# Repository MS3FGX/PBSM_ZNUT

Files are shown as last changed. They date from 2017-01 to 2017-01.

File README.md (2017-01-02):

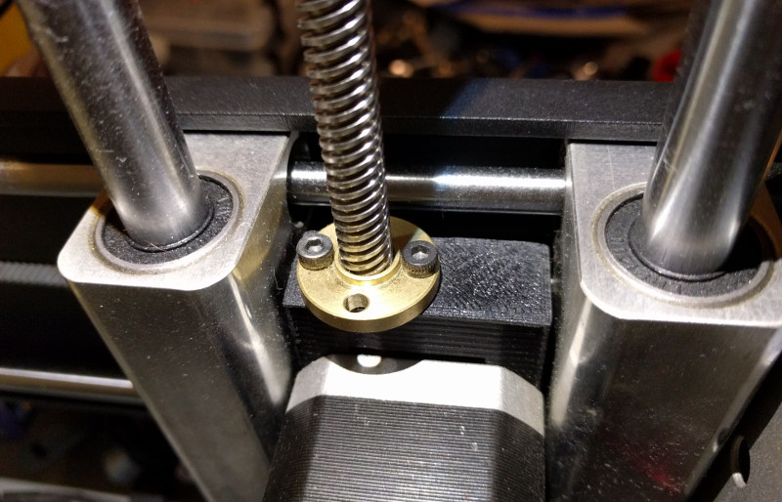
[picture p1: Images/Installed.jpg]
installed


# PrintrBot Simple Metal Metric Z Conversion
With the PrintrBot Simple Metal approaching end of life, I've been thinking ahead in terms of replacement parts. Most of the parts on the PrintrBot are fairly generic or can at least be (relatively) easily swapped out with industry standard components, but one part that really worried me was the Delrin Z nut. This is one of the only parts on the printer that is both proprietary and consumable; eventually the nut will wear down and will need to be replaced.

Rather than buying a bunch of them to stock up for the future (though at the time of this writing, they are no longer available on the PrintrBot store anyway), I decided to replace the Z movement with a standard 8 mm lead screw that can easily be sourced online for a few dollars.

Beyond maintenance and availability issues, converting the PrintrBot's Z motion to metric can (in theory) improve print quality as the controller doesn't have to convert the metric dimensions of the printed part to the PrintrBot's original imperal threaded rod.

# Required Parts
* M3X15mm Cap Screws (x2)
* M3 Nut (x1)
* Brass T8 nut
* 250mm T8 Lead Screw
* 5mmx8mm Coupler (Either printed or purchased)

### Notes:
* Ideally you should get a T8 lead screw that includes a matching nut, but they can be purchased separately if you already have the lead screw.

* If you don't want to buy a Z coupler you can print it, [such as this one from FABlab Moebius](http://www.thingiverse.com/thing:533928).

* Don't be fooled by the length of the original threaded rod (~190mm), with the adapter the Z nut is now above the Y stepper instead of below it, so you need a lead screw that is significantly longer. Otherwise you'll drive the Y arm right off the lead screw if you tried to print something too high.

# Installation
After printing the adapter, press the M3 nut into the bottom and then use the two M3 screws to secure the brass Z nut to the top.

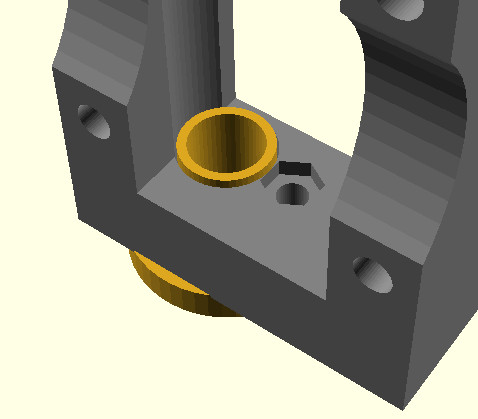
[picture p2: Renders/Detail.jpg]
detail


Once you're sure the brass Z nut fits into the adapter, you can remove the PrintrBot's Y arm, Y belt, and Y stepper. You can then remove the two white spacers, Delrin Z nut, 5mm threaded rod, and Z coupling. They will no longer be required, but I would keep them to be safe.

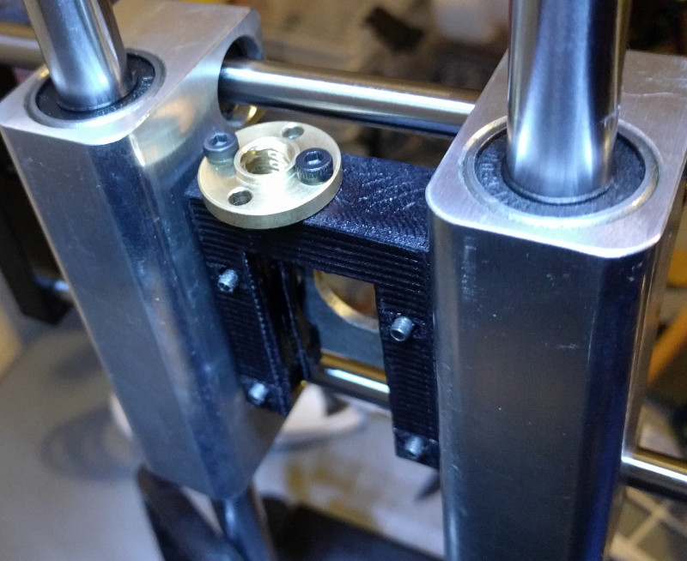
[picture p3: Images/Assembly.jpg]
assembly


Install the adapter and Z nut in place of the original parts, then thread the lead screw through the top of the brass Z nut and down into the new Z coupling.

> **Note**: I found the easiest way to get everything aligned properly was to leave the stepper screws lose while seating the Z coupling and lead screw. Once the coupling and screw are installed properly, then tighten up the stepper screws.

Finally, put the Y stepper and belt back on, making sure that the belt isn't rubbing on the aluminum bearing block (you may need to move the sprocket slightly on the shaft). Also check the belt tightness before putting the Y arm back on.

# Firmware
With the new lead screw installed, you'll need to adjust the printer's firmware so that the steps-per-mm matches the new thread. You can use the [very handy RepRap Calculator](http://www.prusaprinters.org/calculator/#stepspermmlead), but assuming you got a standard 4 start T8 lead screw the steps will need to be set to 400.

To do that, you'll need to connect to the printer with your software of choice and execute the M92 code in the GCode input field. You'll then need to save it to the EEPROM with M500:

```
M92 Z400.00
M500
```

You can then check to make sure it was saved by running M501:

M501

At that point the new values should be active, but I've found in the past it's wise to completely reboot the PrintrBot to make sure firmware settings take.

# Recalibrate Z Offset
After doing so much fiddling with the Z axis, you'll almost certainly need to recalibrate your offset. [Follow the official calibration process](https://www.youtube.com/watch?v=jpmgI4OGldw), and you should be good to do some test prints.

# Auto-Level Warning
As a side effect of this modification, the Z axis movement is now so smooth that the Y arm can actually slide down the rods from just its own weight.

This isn't really a problem normally, but I've found that if you then try and disable the PrintrBot's auto-leveling routine, the arm can actually fall back down while printing. This is evident by smashed up layers and the nozzle occasionally hitting the print. The issue appears to be that the controller turns off the Z stepper between layer changes unless the auto-leveling is actively moving it around.

The easy solution is to just not disable the auto-level routine. The "proper" solution appears to be editing the firmware to tell it to always keep the Z stepper energized; but unless you _really_ want to turn off the leveling, it probably isn't worth it.

# Modifications
The OpenSCAD source is included if you need to make any tweaks to the adapter, but you'll need to drop the ["nutsnbolts" OpenSCAD library](https://github.com/JohK/nutsnbolts) into the current directory before it will compile.

# Acknowledgements
- Makes use of Johannes Kneer's fantastic "nutsnbolts" library.
- Inspired by a design posted by ["aricnorine" on YouImagine](https://www.youmagine.com/designs/printrbot-simple-metal-z-axis-block-for-8mm-metric-coupler).

# License
This program is free software; you can redistribute it and/or modify it under the terms of the GNU General Public License version 3 as published by the Free Software Foundation.



This program is distributed in the hope that it will be useful, but WITHOUT ANY WARRANTY; without even the implied warranty of MERCHANTABILITY or FITNESS FOR A PARTICULAR PURPOSE.

For details, see the file "COPYING" in the source directory.

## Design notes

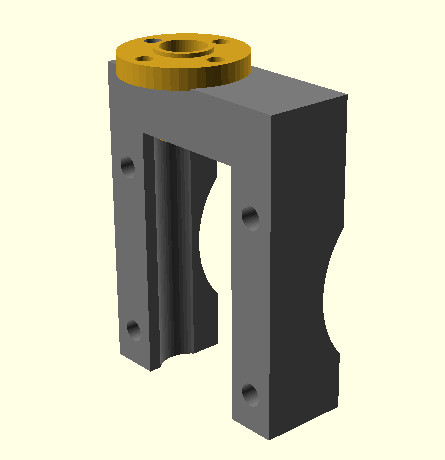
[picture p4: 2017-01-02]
Renders/Overview.jpg

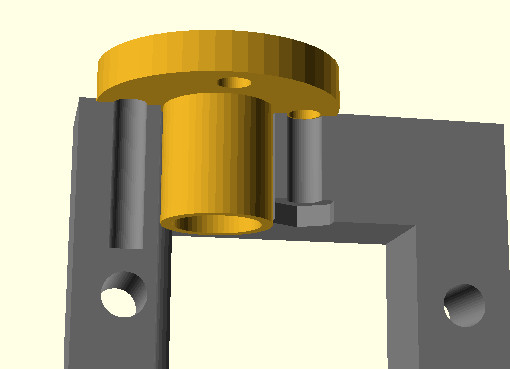
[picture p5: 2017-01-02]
Renders/Internal.jpg

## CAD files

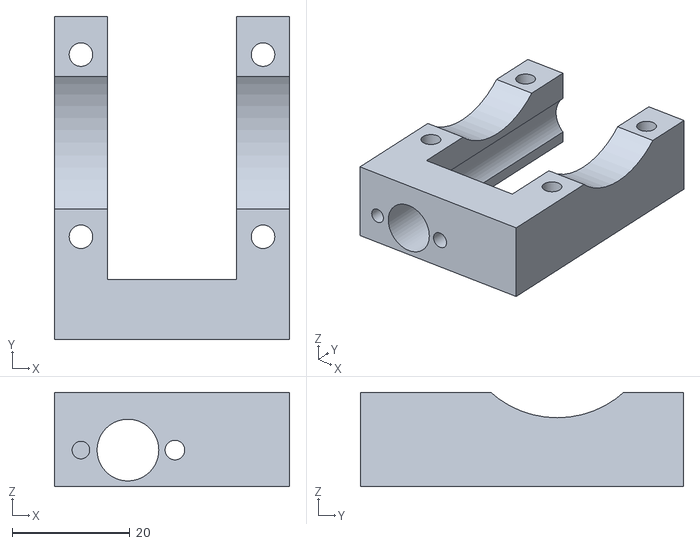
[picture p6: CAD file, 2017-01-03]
pbsm_znut.stl
40.0 x 55.0 x 16.0

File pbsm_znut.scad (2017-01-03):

// PrintrBot Simple Metal 8mm Z Nut
// Increase resolution
$fn=50;

// Pull in nut/bolt library
include <nutsnbolts/cyl_head_bolt.scad>;

// Tolerance
buff = .5;

// Main dimensions
base_z = 55;
base_x = 40; 
base_y = 16;
void_y = base_y + 2;
void_x = base_x - 18;
void_z = (base_z * 1.5);

// Mounting holes
nema_dia = 4;
screw_dia = 3;
trap_depth = 2;

// Brass nut analog
bn_dia = 10;
bn_z = 15;
bn_f_z = 3.6;
bn_f_dia = 22;

module brass_nut()
{
    color("Goldenrod")
    {
        difference()
        {   
            union()
            {
                cylinder(h=bn_z, r=(bn_dia / 2), center=true);
                translate([0, 0, 5])
                    cylinder(h=bn_f_z, r=(bn_f_dia / 2), center=true);
            }   
            
            // Center opening
            cylinder(h=(bn_z + 5), r=4, center=true);
            
            // Screw holes
            translate([8, 0, 0])
                cylinder(h=(bn_z + 5), r=1.5, center=true);
            translate([-8, 0, 0])
                cylinder(h=(bn_z + 5), r=1.5, center=true);             
            translate([0, 8, 0])
                cylinder(h=(bn_z + 5), r=1.5, center=true);
            translate([0, -8, 0])
                cylinder(h=(bn_z + 5), r=1.5, center=true); 
        }
    }
}

module nema_mount()
{
    translate([8, 0, -14])
        rotate([90, 0, 0])
            cylinder(h=(base_y * 1.5), r=(nema_dia / 2), center=true);
    
    translate([-23, 0, -14])
        rotate([90, 0, 0])
            cylinder(h=(base_y * 1.5), r=(nema_dia / 2), center=true);
     
    translate([8, 0, -45])
        rotate([90, 0, 0])
            cylinder(h=(base_y * 1.5), r=(nema_dia / 2), center=true);
    
    translate([-23, 0, -45])
        rotate([90, 0, 0])
            cylinder(h=(base_y * 1.5), r=(nema_dia / 2), center=true);    
}

module body()
{
    cube([base_x, base_y, base_z], center=true);
}

module brass_void()
{
    cylinder(h=(base_z * 3), r=((bn_dia / 2) + (buff / 2)), center=true);
}

module mounting_holes()
{
    translate([8, 0, 0])
        cylinder(h=(bn_z + 5), r=(screw_dia / 2), center=true);

    translate([-8, 0, 0])
    {
        cylinder(h=(bn_z + 5), r=(screw_dia / 1.8), center=true);  
        translate([0, 0, -4.8])
            rotate([0, 0, 90])
                nutcatch_parallel("M3", l=trap_depth);
    }
}

module outer_shape()
{
    translate([-7.5, -1.8, -24])
    {
        difference()
        {
            body();
        
            translate([0, 0, -24])
                cube([void_x, void_y, void_z], center=true);
        }
    }
}

module z_nut()
{
    difference()
    {
        outer_shape();
        brass_void();
        nema_mount();
        mounting_holes();
    }
}

// Rendering
//brass_nut();
rotate([90, 180, 0]) // Rotate for final STL export
difference()
{
    z_nut();
    
    translate([-8, -22.5, -30]) rotate([90, 0, 90])
        cylinder(h=55, r=17, center=true);      
}
// EOF

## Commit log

2017-01-02 Init commit
    [pbsm_znut.scad, pbsm_znut.stl]
2017-01-03 Rotate STL to ideal print orientation
    [pbsm_znut.scad, pbsm_znut.stl]
